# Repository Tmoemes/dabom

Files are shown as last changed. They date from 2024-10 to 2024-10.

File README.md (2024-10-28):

# Installation and Assembly Guide

## Disclaimer

The project was created by a team of students under the Adaptive Robotics minor at Fontys University of Applied Sciences. The goal of the project was to create a plug-and-play introduction to ROS 2 Humble and mobile robotics. By following the guide, anyone should be able to create their own holonomic platform and install all the necessary programs to create a map of the environment and autonomously navigate within the map.

## Hardware Guide

### 3D Printed Parts

All the 3D models are located inside the `CAD` folder. For 3D printing, use the `.stl` file format. You may use Fusion 360 to open the individual components and save them as `.stl`. STL (Standard Triangle Library) files are the most commonly used file format for 3D printing. These files need to be sliced by slicing software before the 3D printer can interpret them. For slicing, Cura slicer is recommended with the following print parameters:

| Print Parameters | Value |
| --- | --- |
| Material | Generic PLA |
| Print Temperature | 205°C |
| Print Speed | 50 mm/s or less (aim for good quality) |
| Layer Height | 0.1 or 0.12 mm |
| Wall Count | 3 |
| Bottom and Top Wall Count | 8 |
| Infill | 20% gyroid |
| Build Plate Adhesion | Brim (recommended) |

For printing, Ultimaker and Bambu Lab printers were used. These printers provide high quality; however, they are not mandatory for the project since the plastic parts are plenty strong by themselves.

For the mechanical assembly, a full CAD assembly is provided, which can be used as a reference.

### Electrical Components

All the necessary components are listed in the BOM (Bill of Materials) Excel file. A possible vendor is provided, but you are free to source the components from anywhere. It is important to mention that the Lidar used for this project, RPLidar model A2M8, is currently discontinued. The alternative A2M12 requires changes to the code. These changes are not implemented in the current working repository! The implementation of the A2M12 model is only recommended for experienced ROS users.

### Electrical Schematics



For the wiring of the power lines it is recommended to use the 0.5mm gauge wires with Farrell connectors on the end to make connections more safe and reliable. 
For details regarding the Arduino check [Arduino Wiring Schematics](Arduino_Code/README.md).

## Software Guide

### Computer Side
On the computer you want to install Ubuntu Desktop 22.04 LTS. For a guide how to install Ubuntu follow the link: [Install Ubuntu Guide](https://itsfoss.com/install-ubuntu/)Additionally it is recommended to download the Raspberry Pi etcher tool and use that instead of Rufus or Balena etcher since that tool will be necessary later for the Raspberry Pi imaging.

First we need to install git
```bash
sudo apt install git
```
Now we can go ahead and download the git

**Follow here from the Raspberry Pi**
The first step is to clone the GitHub repository:
```bash
git clone https://github.com/Tmoemes/dabom.git
```
Now that the GitHub is cloned we can show the folder and navigate within it. 

**It is important to install ROS 2 Humble which you can do by follow this guide [ROS Humble](https://docs.ros.org/en/humble/Installation/Ubuntu-Install-Debs.html) .  Make sure you install the desktop version on both.**

After which we need to install additional components for the system so run the following command: 
```bash
cd dabom
bash install.sh
```
During the installation prompts will pop up, by pressing enter you can continue the installation. Once it is done it is recommended to add the following line to the last line of the .bashrc file. 
```bash
ls -a 
nano .bashrc
```
and add the following line to the end of the text:
```bash 
source /opt/ros/humble/setup.bash
```

Once that is done we are going to navigate into the project and Colcon build it. Colcon building will make sure that the code is built into a ROS package, that can be run. Optionally a parameter could be added to the Colcon build, this way the project does not need to be recompiled after every change of the code.  
```bash 
cd dabom/dabom_ws
colcon build 
```
Optional:
```bash
cd dabom/dabom_ws
colcon build --symlink-install
```

After the build is finished you want to source the install file of the project. Make sure you are in the `dabom_ws` folder.
```bash
source install/setup.bash
```

Optionally you may also add this line to the `.bashrc` file. Just make sure you add the full location. Which means the line will look like this:
```bash
source dabom/dabom_ws/install/setup.bash
```
**End Raspberry Pi installation here**

Now we need to edit the startup file. Navigate to `dabom/dabom_ws/src/dabom_bringup/config` and edit the following file `/launch_config.yaml`. There you may enable or disable certain parts of the system. For example you may disable the external control input for the movement of the robot.

Now we can run the code on the computer side
```bash
ros2 launch dabom_bringup computer_bringup.py
```

### Raspberry Pi Side
[Ubuntu Installation Guide For Windows](https://roboticsbackend.com/install-ubuntu-on-raspberry-pi-without-monitor/)
Follow the installation manual and install Ubuntu Server 22.04.5 LTS onto an SD card. During the installation make sure that SSH is enabled. Make sure to remember the password! You can do this by overwriting the setting before installation. Further more make sure the Wi-Fi details are set to the address of a Wi-Fi network that both the computer/laptop and the Raspberry Pi will be connected to. For the Wi-Fi network it is possible to use a home router or a mobile hotspot with internet access enabled.  Once the installation is done plug in the SD card into the Raspberry Pi and provide power to the system.

Now connect your Ubuntu device to the same Wi-Fi network. Now it is necessary to figure out the IP address of the Raspberry PI. [How to discover devices on network?](https://www.tomshardware.com/how-to/scan-for-network-devices)
Now connect to the raspberry pi via SSH:
```bash
sudo ssh nameofthepi@ipaddress
```

Example:
```bash
sudo ssh pi@192.168.91.2
```

Now that we are in the Raspberry Pi terminal follow the same instructions as the Computer side.  

Before running the programs we have to make sure that the program has access to the serial ports, both for the lidar and the serial communication. Here make sure that the Lidar is plugged into ttyUSB0. On the Raspberry Pi that port is the top USB port furthest away from the Ethernet connector. 
For the Lidar:
```bash
cd src/rpldiar_ros/
source scripts/create_udev_rules.sh
```
For the serial communication:
```bash
cd dabom/dabom_ws/src/serial_comm
bash create_udev_rules.sh
```

If this would not work for some reason you may also run the following commands as a backup:
```bash
sudo chmod 777 /dev/ttyUSB0
sudo chmod 777 /dev/ttyS0
```

Now that the permissions are settled we can proceed with the launching of the robot software! Furthermore for some reason TAB auto complete is not working on the following command. Do this from inside the `dabom_ws` folder.
```bash
source /opt/ros/humble/setup.bash
source install/setup.bash
ros2 launch dabom_bringup rpi_bringup.py
```
If no error is returned the robot code should be up and running, you may exit the code any time by pressing `Ctrl + C` . 

# Operation of the robot:
Depending on which modes you enable in the startup file the robot can be controlled by an Xbox controller. As well as by RVIZ2, which is a GUI automatically turned on when you launch the computer side bring up. In RVIZ2 you may set Nav2 Goals, if you do so the robot navigates there autonomously.

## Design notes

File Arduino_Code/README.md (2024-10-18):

# Hardware Installation Instructions
## Software install
### Step-by-Step Guide to Install and Upload the Project using PlatformIO

1. **Install PlatformIO:**
    - Download and install [Visual Studio Code](https://code.visualstudio.com/).
    - Open Visual Studio Code and go to the Extensions view by clicking on the square icon in the sidebar or pressing `Ctrl+Shift+X`.
    - Search for "PlatformIO IDE" and click "Install".

2. **Open the Project in Visual Studio Code:**
    - Open Visual Studio Code.
    - Click on `File` > `Open Folder...` and select the `Arduino_Code` directory from the cloned repository.

3. **Install Dependencies:**
    - Open the PlatformIO Home by clicking on the house icon in the sidebar.
    - Click on "Open Project" and select the `Arduino_Code` directory.
    - PlatformIO will automatically detect the `platformio.ini` file and install the necessary dependencies.

4. **Configure the Project:**
    - Open the `platformio.ini` file in the `Arduino_Code` directory.
    - Ensure the configuration matches your setup. For example:
      ```ini
      [env:megaatmega2560]
        platform = atmelavr
        board = megaatmega2560
        framework = arduino
        monitor_speed = 19200
        lib_deps = 
	        paulstoffregen/Encoder@^1.4.4
      ```

5. **Upload the Code to Arduino Mega:**
    - Connect your Arduino Mega to your computer using a USB cable.
    - In Visual Studio Code, open the PlatformIO sidebar by clicking on the alien icon.
    - Click on the "Upload" button (arrow pointing right) to compile and upload the code to the Arduino Mega.

6. **Monitor Serial Output (Optional):**
    - To monitor the serial output from the Arduino, click on the "Serial Monitor" button (plug icon) in the PlatformIO sidebar.
    - Ensure the baud rate matches the one set in your code (e.g., `19200`).

Your project should now be uploaded to the Arduino Mega and running as expected.

## Wiring for Power and Signals

### Arduino <-> Raspberry Pi Communication
The Pi and Arduino communicate using the hardware serial of the Pi to the Serial2 of the Arduino Mega.
In this case we are also powering the Arduino from the Pi 5V pins.
Make sure the Pi and Arduino are grounded together for serial communication to funcion properly 
1. **Raspberry Pi GPIO Connections:**
    - `GPIO 14 (TXD)` to `Arduino Pin 16 (TX2)`
    - `GPIO 15 (RXD)` to `Arduino Pin 17 (RX2)`

### Example Wiring Diagram for Arduino <-> Raspberry Pi Communication
```
+------------------+       +------------------+
| Raspberry Pi     |       | Arduino Mega     |
|                  |       |                  |
|   GPIO 14 (TXD)  +------>+ 17 (RX2)         |
|   GPIO 15 (RXD)  +------>+ 16 (TX2)         |
+------------------+       +------------------+
```

### Motor and Encoder Connections
For the motors, it is necessary to connect the `EN` connection to PWM-capable pins to modulate speed. On the Arduino Mega, the PWM-capable pins are `D2-D13` and `D44-D46`.

For the encoders, it is important to connect at least one of the channels to an interrupt-capable pin. The Arduino Mega has 6 available interrupts:
- `INT.0` on Pin `21`
- `INT.1` on Pin `20`
- `INT.2` on Pin `19`
- `INT.3` on Pin `18`
- `INT.4` on Pin `2`
- `INT.5` on Pin `3`

Make sure the Arduino is grounded together with the motor drivers and the encoders to ensure proper signaling.

1. **Motor Connections:**  
    - **Motor 0 (Front Left):**
        - `EN` pin to `D2`
        - `IN1` pin to `D35`
        - `IN2` pin to `D37`
    - **Motor 1 (Front Right):**
        - `EN` pin to `D3`
        - `IN1` pin to `D41`
        - `IN2` pin to `D39`
    - **Motor 2 (Back Left):**
        - `EN` pin to `D4`
        - `IN1` pin to `D31`
        - `IN2` pin to `D33`
    - **Motor 3 (Back Right):**
        - `EN` pin to `D5`
        - `IN1` pin to `D45`
        - `IN2` pin to `D43`

2. **Encoder Connections:**
    - **Encoder 0 (Front Left):**
        - `A` pin to `D18`
        - `B` pin to `D23`
    - **Encoder 1 (Front Right):**
        - `A` pin to `D19`
        - `B` pin to `D25`
    - **Encoder 2 (Back Left):**
        - `A` pin to `D20`
        - `B` pin to `D27`
    - **Encoder 3 (Back Right):**
        - `A` pin to `D21`
        - `B` pin to `D29`

### Example Wiring Diagram for Motors and Encoders
```
+------------------+       +------------------+
| Motor 0          |       | Arduino          |
|                  |       |                  |
|   EN             +------>+ D2               |
|   IN1            +------>+ D35              |
|   IN2            +------>+ D37              |
+------------------+       +------------------+

+------------------+       +------------------+
| Encoder 0        |       | Arduino          |
|                  |       |                  |
|   A              +------>+ D18              |
|   B              +------>+ D23              |
+------------------+       +------------------+

+------------------+       +------------------+
| Motor 1          |       | Arduino          |
|                  |       |                  |
|   EN             +------>+ D3               |
|   IN1            +------>+ D41              |
|   IN2            +------>+ D39              |
+------------------+       +------------------+

+------------------+       +------------------+
| Encoder 1        |       | Arduino          |
|                  |       |                  |
|   A              +------>+ D19              |
|   B              +------>+ D25              |
+------------------+       +------------------+

+------------------+       +------------------+
| Motor 2          |       | Arduino          |
|                  |       |                  |
|   EN             +------>+ D4               |
|   IN1            +------>+ D31              |
|   IN2            +------>+ D33              |
+------------------+       +------------------+

+------------------+       +------------------+
| Encoder 2        |       | Arduino          |
|                  |       |                  |
|   A              +------>+ D20              |
|   B              +------>+ D27              |
+------------------+       +------------------+

+------------------+       +------------------+
| Motor 3          |       | Arduino          |
|                  |       |                  |
|   EN             +------>+ D5               |
|   IN1            +------>+ D45              |
|   IN2            +------>+ D43              |
+------------------+       +------------------+

+------------------+       +------------------+
| Encoder 3        |       | Arduino          |
|                  |       |                  |
|   A              +------>+ D21              |
|   B              +------>+ D29              |
+------------------+       +------------------+
```

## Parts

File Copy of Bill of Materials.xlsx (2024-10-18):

Bill of Material
Item # | Description | Vendor | Part Number | Qty | Cost | Link to Where to Purchase
1 | Arduino Uno R3 with DIP | Amazon | Uno R3 | 1 | $21.95 | http://www.amazon.com/Arduino-UNO-board-DIP-ATmega328P/dp/B006H06TVG
2 | raspberry pi 4 8gb |  |  | 1 | $81.77
3 | Mechanum wheels | Amazon |  | 4 | $29.95 | https://www.amazon.nl/Mecanum-wiel-omni-directionele-Auto-onderdelen-Accessoires-DIY-speelgoedcomponenten/dp/B08VFLDJR9
4 | RPlidar | Amazon | A2M8 | 1 | $599.54 | https://www.amazon.nl/-/en/RPLIDAR-A2M8-360%C2%B0-laser-scanner/dp/B01L1T32PI
5 | RPlidar (Potential replacement due to retirement of A2m8 LIDAR) | antratek | A2M12 | 1 | $277.99 | https://www.antratek.nl/rplidar-a2m12-360-laser-range-scanner
6 | l298n motor driver |  |  | 2 | $6.99 | https://www.amazon.nl/DollaTek-Stepper-Controller-verdubbeling-Smart-auto-robot/dp/B07DK6Q8F9
7 | BUCK converter at least 5A | Amazon |  | 1 | $7,49 | https://www.amazon.nl/JZK-Verstelbare-Converter-constante-Regulator/dp/B09TT1Q739
8 | 0,5mm wires |  |  | ~2m
9 | Male to Female Dupont jumper wires |  |  | 40 | $7.99 | https://www.amazon.nl/Dupont-Jumper-Arduino-Raspberry-projects/dp/B09KGRM98K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

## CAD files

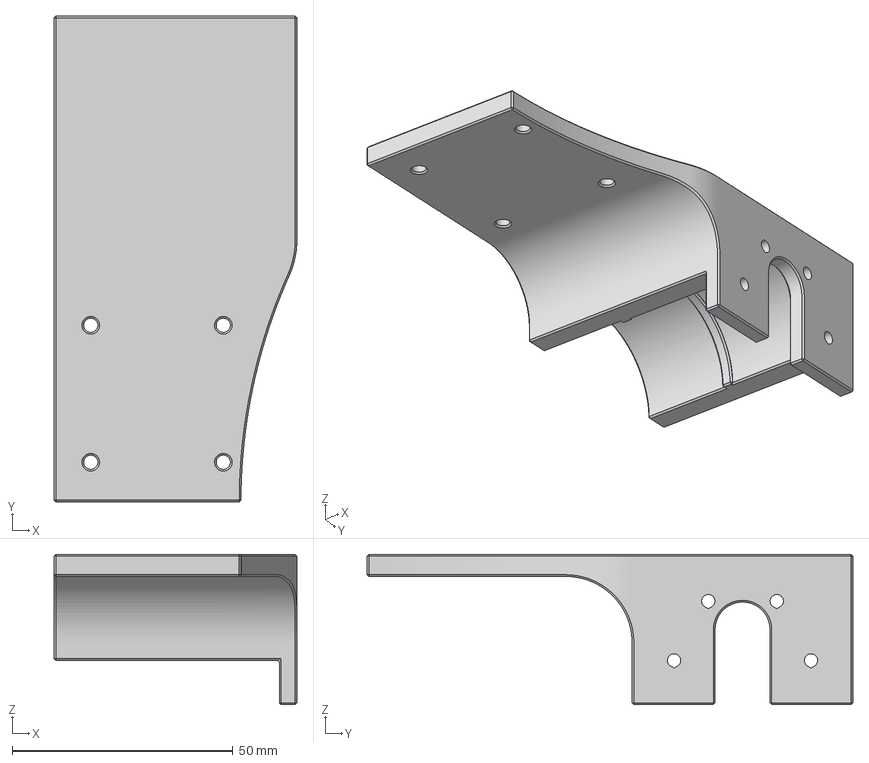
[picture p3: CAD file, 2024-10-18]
CAD/MotorMountD.3mf
55.0 x 110.0 x 34.0 mm

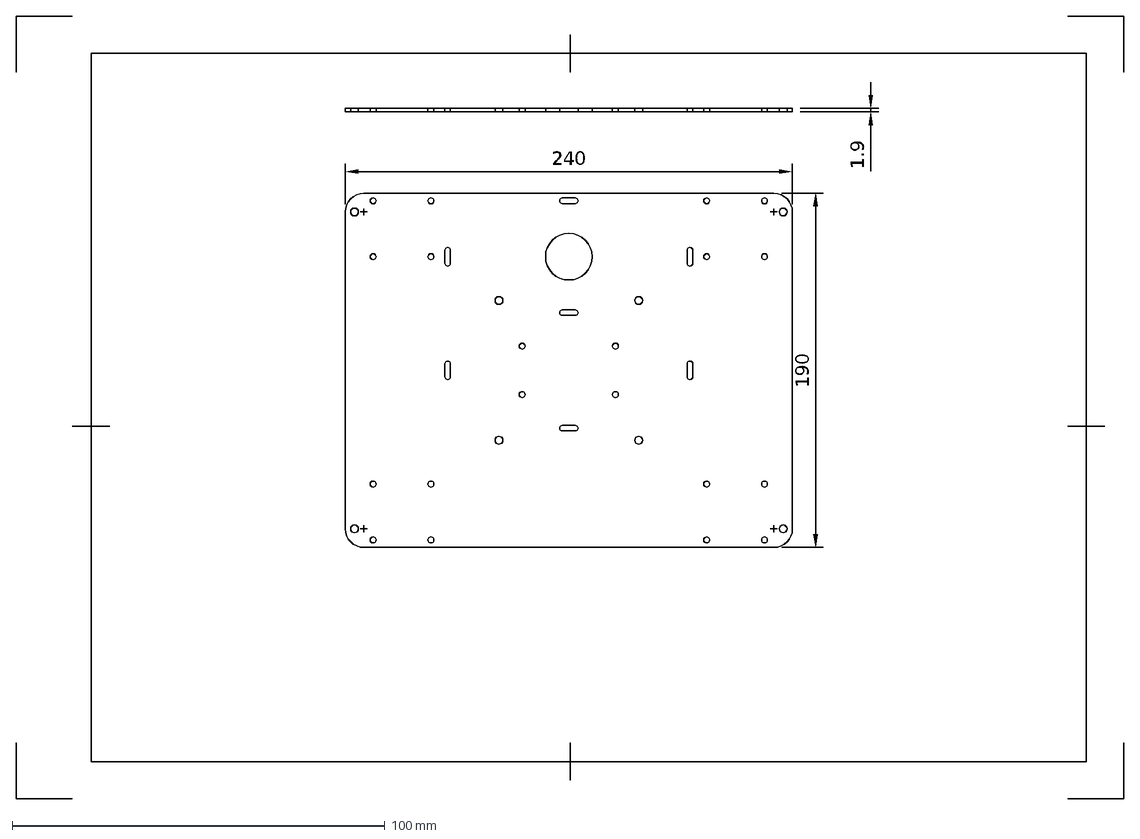
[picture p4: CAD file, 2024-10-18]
CAD/Base_Plate.dxf
240
190
1.9

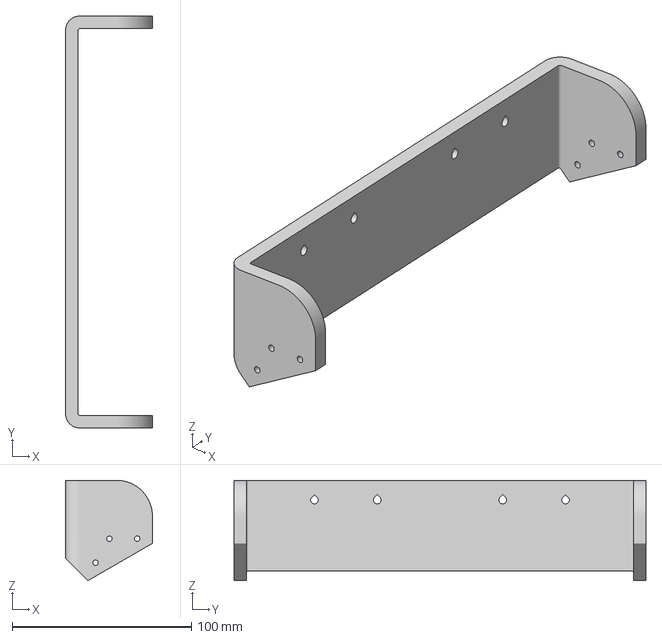
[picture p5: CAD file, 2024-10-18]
CAD/C_Karg_Brace.3mf
48.4 x 229.8 x 56.0 mm

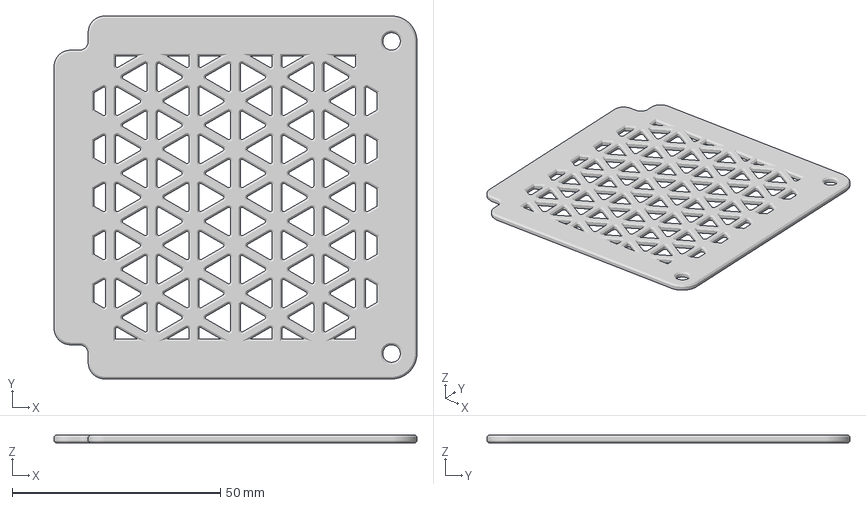
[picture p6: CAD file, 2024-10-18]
CAD/WirePlate.3mf
87.2 x 87.2 x 2.00 mm

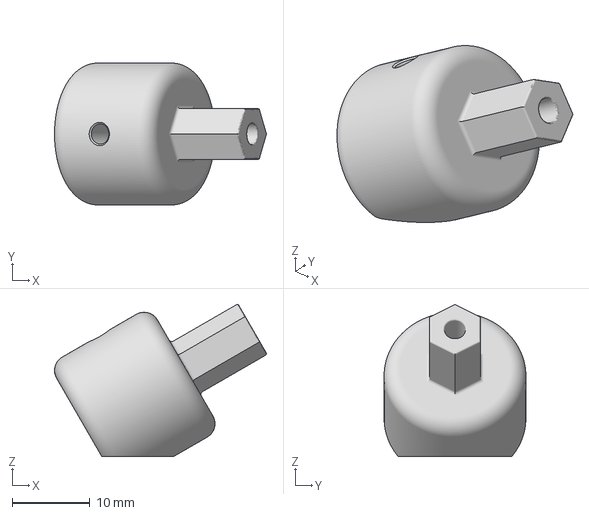
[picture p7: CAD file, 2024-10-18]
CAD/WheelHubAddapter2.6mmHole.3mf
27.3 x 18.2 x 19.6 mm

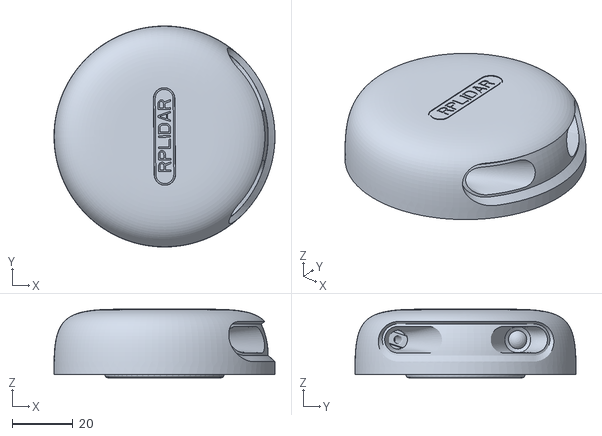
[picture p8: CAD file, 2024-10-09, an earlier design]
dabom_ws/src/dabomb_description/meshes/LIDAR_1.stl
72.5 x 72.5 x 22.5

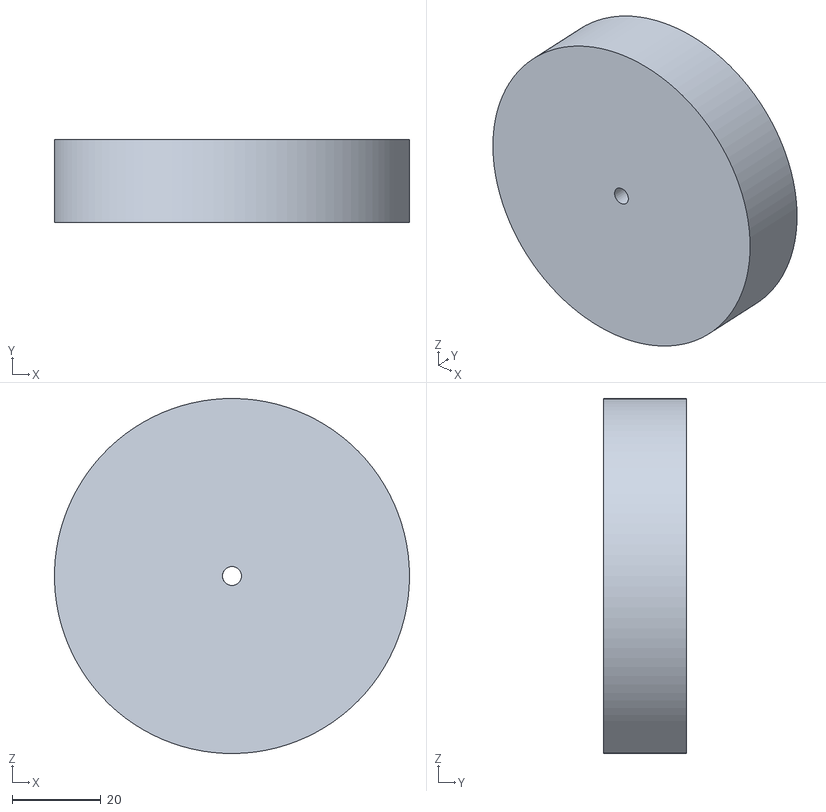
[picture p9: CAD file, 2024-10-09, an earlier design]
dabom_ws/src/dabomb_description/meshes/Wheel2_1.stl
80.0 x 18.7 x 80.0

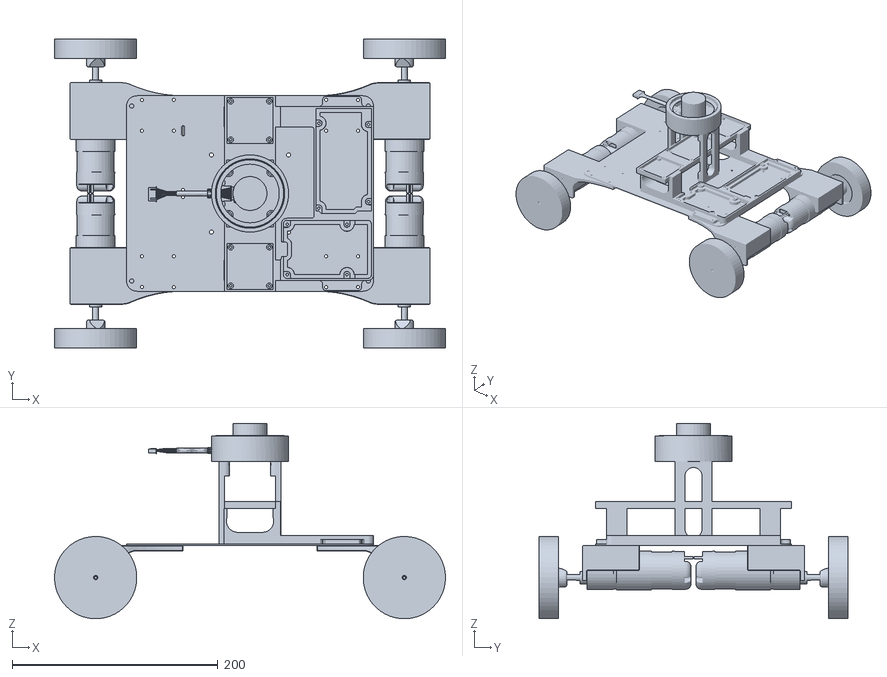
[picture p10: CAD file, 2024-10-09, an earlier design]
dabom_ws/src/dabomb_description/meshes/base_link.stl
380.0 x 300.0 x 190.0

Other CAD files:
dabom_ws/src/install/dabomb_description/share/dabomb_description/meshes/LIDAR_1.stl
dabom_ws/src/install/dabomb_description/share/dabomb_description/meshes/base_link.stl
CAD/MotorMountB.3mf
dabom_ws/src/install/dabomb_description/share/dabomb_description/meshes/Wheel4_1.stl
CAD/MotorMountA.3mf
dabom_ws/src/install/dabomb_description/share/dabomb_description/meshes/Wheel3_1.stl
CAD/MotorMountC.3mf
dabom_ws/src/install/dabomb_description/share/dabomb_description/meshes/Wheel2_1.stl
dabom_ws/src/install/dabomb_description/share/dabomb_description/meshes/Wheel1_1.stl
dabom_ws/src/dabomb_description/meshes/Wheel4_1.stl
CAD/Base_Plate.dwg
dabom_ws/src/dabomb_description/meshes/Wheel1_1.stl
dabom_ws/src/dabomb_description/meshes/Wheel3_1.stl

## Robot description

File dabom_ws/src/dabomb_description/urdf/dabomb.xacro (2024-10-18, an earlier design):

<?xml version="1.0" ?>
<robot name="dabomb" xmlns:xacro="http://www.ros.org/wiki/xacro">

<material name="gray">
  <color rgba="0.75 0.75 0.75 1.0"/>  <!-- This is gray with full opacity -->
</material>


<xacro:include filename="$(find dabomb_description)/urdf/materials.xacro" />
<xacro:include filename="$(find dabomb_description)/urdf/dabomb.trans" />
<xacro:include filename="$(find dabomb_description)/urdf/dabomb.gazebo" />
<link name="base_footprint" />

<link name="base_link">
  <inertial>
    <origin xyz="0.001965778230803289 0.00012164122075361151 0.06076837613584456" rpy="0 0 0"/>
    <mass value="3.2995710672768235"/>
    <inertia ixx="0.032808" iyy="0.061307" izz="0.086932" ixy="-3.2e-05" iyz="-8e-06" ixz="-8.9e-05"/>
  </inertial>
  <visual>
    <origin xyz="0 0 -0.04" rpy="0 0 0"/>
    <geometry>
      <mesh filename="file://$(find dabomb_description)/meshes/base_link.stl" scale="0.001 0.001 0.001"/>
    </geometry>
    <material name="gray"/>
  </visual>
  <collision>
    <origin xyz="0 0 -0.04" rpy="0 0 0"/>
    <geometry>
      <mesh filename="file://$(find dabomb_description)/meshes/base_link.stl" scale="0.001 0.001 0.001"/>
    </geometry>
  </collision>
</link>

<link name="Wheel1_1">
  <inertial>
    <origin xyz="3.605747672386084e-07 0.00934999998147884 -8.583050173371909e-10" rpy="0 0 0"/>
    <mass value="0.7357403909763499"/>
    <inertia ixx="0.000317" iyy="0.00059" izz="0.000317" ixy="-0.0" iyz="0.0" ixz="0.0"/>
  </inertial>
  <visual>
    <origin xyz="-0.15 -0.15 -0.04" rpy="0 0 0"/>
    <geometry>
      <mesh filename="file://$(find dabomb_description)/meshes/Wheel1_1.stl" scale="0.001 0.001 0.001"/>
    </geometry>
    <material name="gray"/>
  </visual>
  <collision>
    <origin xyz="-0.15 -0.15 -0.04" rpy="0 0 0"/>
    <geometry>
      <mesh filename="file://$(find dabomb_description)/meshes/Wheel1_1.stl" scale="0.001 0.001 0.001"/>
    </geometry>
  </collision>
</link>

<link name="Wheel3_1">
  <inertial>
    <origin xyz="-3.6057476762718643e-07 0.00934999998147884 -8.583049965205092e-10" rpy="0 0 0"/>
    <mass value="0.7357403909763499"/>
    <inertia ixx="0.000317" iyy="0.00059" izz="0.000317" ixy="-0.0" iyz="0.0" ixz="0.0"/>
  </inertial>
  <visual>
    <origin xyz="0.15 -0.15 -0.04" rpy="0 0 0"/>
    <geometry>
      <mesh filename="file://$(find dabomb_description)/meshes/Wheel3_1.stl" scale="0.001 0.001 0.001"/>
    </geometry>
    <material name="gray"/>
  </visual>
  <collision>
    <origin xyz="0.15 -0.15 -0.04" rpy="0 0 0"/>
    <geometry>
      <mesh filename="file://$(find dabomb_description)/meshes/Wheel3_1.stl" scale="0.001 0.001 0.001"/>
    </geometry>
  </collision>
</link>

<link name="Wheel2_1">
  <inertial>
    <origin xyz="3.605747672386084e-07 -0.00934999998147884 -8.583056140820666e-10" rpy="0 0 0"/>
    <mass value="0.7357403909763499"/>
    <inertia ixx="0.000317" iyy="0.00059" izz="0.000317" ixy="0.0" iyz="-0.0" ixz="-0.0"/>
  </inertial>
  <visual>
    <origin xyz="-0.15 0.15 -0.04" rpy="0 0 0"/>
    <geometry>
      <mesh filename="file://$(find dabomb_description)/meshes/Wheel2_1.stl" scale="0.001 0.001 0.001"/>
    </geometry>
    <material name="gray"/>
  </visual>
  <collision>
    <origin xyz="-0.15 0.15 -0.04" rpy="0 0 0"/>
    <geometry>
      <mesh filename="file://$(find dabomb_description)/meshes/Wheel2_1.stl" scale="0.001 0.001 0.001"/>
    </geometry>
  </collision>
</link>

<link name="Wheel4_1">
  <inertial>
    <origin xyz="-3.6057476762718643e-07 -0.00934999998147884 -8.583055516320215e-10" rpy="0 0 0"/>
    <mass value="0.7357403909763499"/>
    <inertia ixx="0.000317" iyy="0.00059" izz="0.000317" ixy="0.0" iyz="-0.0" ixz="-0.0"/>
  </inertial>
  <visual>
    <origin xyz="0.15 0.15 -0.04" rpy="0 0 0"/>
    <geometry>
      <mesh filename="file://$(find dabomb_description)/meshes/Wheel4_1.stl" scale="0.001 0.001 0.001"/>
    </geometry>
    <material name="gray"/>
  </visual>
  <collision>
    <origin xyz="0.15 0.15 -0.04" rpy="0 0 0"/>
    <geometry>
      <mesh filename="file://$(find dabomb_description)/meshes/Wheel4_1.stl" scale="0.001 0.001 0.001"/>
    </geometry>
  </collision>
</link>

<link name="laser">
  <inertial>
    <origin xyz="0.0039907248324316845 -0.00022724344297910342 -0.002459373991692604" rpy="0 0 0"/>
    <mass value="0.2649835736448253"/>
    <inertia ixx="8.2e-05" iyy="8.5e-05" izz="0.000145" ixy="-0.0" iyz="0.0" ixz="-2e-06"/>
  </inertial>
  <visual>
    <origin xyz="0.0 -0.0 -0.19" rpy="0 0 0"/>
    <geometry>
      <mesh filename="file://$(find dabomb_description)/meshes/LIDAR_1.stl" scale="0.001 0.001 0.001"/>
    </geometry>
    <material name="gray"/>
  </visual>
  <collision>
    <origin xyz="0.0 -0.0 -0.19" rpy="0 0 0"/>
    <geometry>
      <mesh filename="file://$(find dabomb_description)/meshes/LIDAR_1.stl" scale="0.001 0.001 0.001"/>
    </geometry>
  </collision>
</link>

<joint name="base_joint" type="fixed">
  <origin xyz="0.0 0.0 0.04" rpy="0 0 0"/>
  <parent link="base_footprint"/>
  <child link="base_link"/>
</joint>

<joint name="Wheel1" type="continuous">
  <origin xyz="0.15 0.15 0.0" rpy="0 0 0"/>
  <parent link="base_link"/>
  <child link="Wheel1_1"/>
  <axis xyz="-0.0 1.0 0.0"/>
</joint>

<joint name="Wheel3" type="continuous">
  <origin xyz="-0.15 0.15 0.0" rpy="0 0 0"/>
  <parent link="base_link"/>
  <child link="Wheel3_1"/>
  <axis xyz="0.0 1.0 0.0"/>
</joint>

<joint name="Wheel2" type="continuous">
  <origin xyz="0.15 -0.15 0.0" rpy="0 0 0"/>
  <parent link="base_link"/>
  <child link="Wheel2_1"/>
  <axis xyz="-0.0 -1.0 0.0"/>
</joint>

<joint name="Wheel4" type="continuous">
  <origin xyz="-0.15 -0.15 0.0" rpy="0 0 0"/>
  <parent link="base_link"/>
  <child link="Wheel4_1"/>
  <axis xyz="0.0 -1.0 0.0"/>
</joint>

<joint name="laser_joint" type="fixed">
  <origin xyz="0.0 0.0 0.15" rpy="0 0 ${pi}"/>
  <parent link="base_link"/>
  <child link="laser"/>
</joint>

</robot>

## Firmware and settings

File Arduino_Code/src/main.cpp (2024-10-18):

#include <Arduino.h>
#include "config.h"

void processSerialInput(HardwareSerial &thisserial);
void getSerialInput();
void printMotorInfo();
void sendEncoder();

long currentTime = 0;

// debug output timing
long d_previousTime = 0;

// pi comm timing
long p_previousTime = 0;

long lastReceivedTime = 0;

void setup()
{
  // Used to display debug information
  Serial.begin(DEBUG_BAUD_RATE);

  // Serial for communication with Raspberry Pi
  Serial2.begin(PI_BAUD_RATE);

  lastReceivedTime = millis();
  // Wait for Serial Monitor to be opened
  while (!Serial || !Serial2)
  {
    // do nothing
  }
  Serial.println("Serial Ready");

  for (size_t i = 0; i < 4; i++)
  {
    motors[i].begin();
    Serial.println("Motor ");
    Serial.print(i);
    Serial.println(" started");
  }

  Serial.println("Setup Complete");
}

void loop()
{
  currentTime = millis();

  if (currentTime - d_previousTime >= DEBUG_FREQ && DEBUG_FREQ != 0)
  {
    printMotorInfo();
    d_previousTime = currentTime;
  }

  if (currentTime - lastReceivedTime >= PI_COMM_TIMEOUT)
  {
    Serial.println("No command received, stopping motors");
    lastReceivedTime = currentTime;
    for (int i = 0; i < 4; i++)
    {
      motors[i].stop();
    }
  }

  if (currentTime - p_previousTime >= PI_COMM_FREQ)
  {

    p_previousTime = currentTime;
    sendEncoder();
  }

  // processSerialInput(Serial);
  processSerialInput(Serial2);
}

void processSerialInput(HardwareSerial &thisserial)
{
  if (thisserial.available())
  {
    char input[32] = {0};
    thisserial.readBytesUntil('\n', input, 31);
    input[31] = '\0';                   // Ensure null-terminated string
    char *command = strtok(input, " "); // tokenise input on spaces
    if (command != nullptr && strcmp(command, "m") == 0)
    {
      char *motorStr = strtok(NULL, " ");
      char *speedStr = strtok(NULL, " ");
      if (motorStr != nullptr && speedStr != nullptr)
      {

        unsigned int motor = atoi(motorStr);

        // check if motor number is valid
        if (motor < 0 || motor >= sizeof(motors) / sizeof(Motor))
        {
          Serial.println("Invalid motor number");
          return;
        }

        // convert speed string to double
        double speed = atof(speedStr);

        // map input speed to 0-255
        int targetSpeed = map(abs(speed), 0, 10, 50, 255);

        // set motor speed and direction
        motors[motor].setSpeed(targetSpeed);
        if (speed > 0){motors[motor].forward();}
        else if (speed < 0){motors[motor].backward();}
        else{motors[motor].stop();}

        // update last received time
        lastReceivedTime = currentTime;
      }
      else
      {
        Serial.println("Invalid input format");
      }
    }
    else
    {
      // Serial.print("Unknown command: ");
      // Serial.print(input);
      // Serial.println();
    }
  }
}

void printMotorInfo()
{
  char message[320] = {0};
  int x = snprintf(message, sizeof(message), "\nCurrent motor Values---------------\n");
  for (size_t i = 0; i < 4; i++)
  {
    long count = motors[i].readEncoder();
    double speed = motors[i].getSpeed();
    x += snprintf(message + x, sizeof(message), "Motor %i: \n-Speed: %d \n-Encoder Value: %li\n",i, speed, count);
    Serial.print(message);
  }
}

void sendEncoder()
{
  long count = motors[0].readEncoder();
  long count1 = motors[1].readEncoder();
  long count2 = motors[2].readEncoder();
  long count3 = motors[3].readEncoder();

  char message[64] = {0};
  snprintf(message, sizeof(message), "%li,%li,%li,%li", count, count1, count2, count3);
  Serial2.println(message);
}

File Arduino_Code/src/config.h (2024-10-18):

#ifndef CONFIG_H
#define CONFIG_H
#include "motor.h"
#include <Encoder.h>

// PI COMM constants
#define PI_COMM_FREQ 20
#define PI_COMM_TIMEOUT 300
#define PI_BAUD_RATE 38400

// DEBUG constants
#define DEBUG_FREQ 1000 // time in ms between debug prints, 0 to disable
#define DEBUG_BAUD_RATE 19200

// Motor 0:Front left
#define MOTOR0_PIN_EN 2 
#define MOTOR0_PIN_IN1 35
#define MOTOR0_PIN_IN2 37
#define ENCODER0_PIN_A 18 // INT.3 on Pin 18
#define ENCODER0_PIN_B 23   

// Motor 1: Front right
#define MOTOR1_PIN_EN 3
#define MOTOR1_PIN_IN1 41
#define MOTOR1_PIN_IN2 39
#define ENCODER1_PIN_A 19 // INT.2 on pin 19
#define ENCODER1_PIN_B 25

// Motor 2: Back left
#define MOTOR2_PIN_EN 4
#define MOTOR2_PIN_IN1 31
#define MOTOR2_PIN_IN2 33
#define ENCODER2_PIN_A 20 // INT.1 on pin 20
#define ENCODER2_PIN_B 27
 
// Motor 3: Back right
#define MOTOR3_PIN_EN 5
#define MOTOR3_PIN_IN1 45
#define MOTOR3_PIN_IN2 43
#define ENCODER3_PIN_A 21 // INT.0 on Pin 21
#define ENCODER3_PIN_B 29

// Defining and setting up the motors and encoders
Encoder enc0(ENCODER0_PIN_A, ENCODER0_PIN_B);
Encoder enc1(ENCODER1_PIN_A, ENCODER1_PIN_B);
Encoder enc2(ENCODER2_PIN_A, ENCODER2_PIN_B);
Encoder enc3(ENCODER3_PIN_A, ENCODER3_PIN_B);

Motor m0(MOTOR0_PIN_EN, MOTOR0_PIN_IN1, MOTOR0_PIN_IN2, enc0, true);
Motor m1(MOTOR1_PIN_EN, MOTOR1_PIN_IN1, MOTOR1_PIN_IN2, enc1);
Motor m2(MOTOR2_PIN_EN, MOTOR2_PIN_IN1, MOTOR2_PIN_IN2, enc2, true);
Motor m3(MOTOR3_PIN_EN, MOTOR3_PIN_IN1, MOTOR3_PIN_IN2, enc3);

Motor motors[] = {m0,m1,m2,m3};

#endif // CONFIG_H

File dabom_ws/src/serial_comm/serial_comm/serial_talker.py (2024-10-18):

from geometry_msgs.msg import TwistStamped
import rclpy
from rclpy.node import Node
import serial


class Serial_Talker(Node):

    def __init__(self):
        super().__init__('Serial_Talker')

        # Declare parameters with default values
        self.declare_parameter('timer_period', 0.2)
        self.declare_parameter('port', '/dev/ttyS0')
        self.declare_parameter('baudrate', 38400)
        self.declare_parameter('timeout', 0.01)
        self.declare_parameter('pulses_per_rev', 1440)
        self.declare_parameter('wheel_radius', 0.08)

        # Create a subscription to the /motor_vel topic
        self.subscription = self.create_subscription(TwistStamped, '/motor_vel', self.motor_vel_callback, 1)

        # Create a publisher to the /arduino_vel topic
        self.publisher_ = self.create_publisher(TwistStamped, '/arduino_vel', 1)
        
        # Get the timer period parameter and create a timer
        timer_period = self.get_parameter('timer_period').get_parameter_value().double_value
        self.timer = self.create_timer(timer_period, self.arduino_vel_callback)

        # Get serial communication parameters
        self.port = self.get_parameter('port').get_parameter_value().string_value   
        self.baudrate = self.get_parameter('baudrate').get_parameter_value().integer_value
        self.timeout = self.get_parameter('timeout').get_parameter_value().double_value


        # Initialize serial communication
        self.serial_port = serial.Serial(
            port=self.port,
            baudrate=self.baudrate,
            timeout=self.timeout,
            write_timeout=self.timeout,
        )

        # Initialize variables for velocity calculation
        self.last_time = self.get_clock().now()
        self.pulses_per_rev = self.get_parameter('pulses_per_rev').get_parameter_value().integer_value
        self.wheel_radius = self.get_parameter('wheel_radius').get_parameter_value().double_value
        self.last_encoder_values = [0, 0, 0, 0]

    def arduino_vel_callback(self):
        serial_read = None
        try:
            serial_read = self.serial_port.readline().strip()
            # self.get_logger().info('receiving: "%s"' % serial_read)
            
        except serial.SerialException:
            # Log an error if there is an issue reading from the serial port
            self.get_logger().error('Error reading from serial port')
            # Reinitialize the serial port
            self.serial = serial.Serial(
                port=self.port,
                baudrate=self.baudrate,
                timeout=self.timeout,
                write_timeout=self.timeout
            )
        if serial_read:
            try:
                # Parse the encoder values from the serial data
                encoder_values = str(serial_read)[2:-1].split(',')
                if len(encoder_values) != 4:
                    raise Exception('Incorrect number of encoder values')
                for i in range(4):
                    encoder_values[i] = float(encoder_values[i])
            except Exception as e:
                self.get_logger().error('Error parsing serial data')
                return
            # self.get_logger().info('read encoder val: "%s"' % encoder_values)
            calculated_velocities = self.calculate_velocities(encoder_values)
            # self.get_logger().info('calculated vel: "%s"' % calculated_velocities)
            msg = TwistStamped()
            msg.twist.linear.x = calculated_velocities[0]
            msg.twist.linear.y = calculated_velocities[1]
            msg.twist.linear.z = calculated_velocities[2]
            msg.twist.angular.x = calculated_velocities[3]
            self.publisher_.publish(msg)
            

    def calculate_velocities(self, encoder_values):
        current_time = self.get_clock().now()
        delta_time = (current_time - self.last_time).nanoseconds / 1e9
        self.last_time = current_time
        angular_velocities = [0, 0, 0, 0]
        for i in range(4):
            encoder_diff = encoder_values[i] - self.last_encoder_values[i]
            angular_velocities[i] = (encoder_diff / self.pulses_per_rev) * 2 * 3.14159 / delta_time
        self.last_encoder_values = encoder_values
        return angular_velocities
        
    def send_serial_data(self, data):
        if self.serial_port.is_open:
            try:
                # self.serial_port.reset_output_buffer()
                # self.get_logger().info('sending: "%s"' % data.encode())
                self.serial_port.write(data.encode())
            except serial.SerialException:
                self.get_logger().error('Error writing to serial port')
                self.serial = serial.Serial(
                    port=self.port,
                    baudrate=self.baudrate,
                    timeout=self.timeout,
                    write_timeout=self.timeout
                )

    def motor_vel_callback(self, msg):
        motor_vels = [msg.twist.linear.x, msg.twist.linear.y,msg.twist.linear.z, msg.twist.angular.x]
        # Send the message over the serial port
        for i in range(4):
            serial_message = f'm {i} {str(round(motor_vels[i],3))}\n'
            # self.get_logger().info('sending: "%s"' % serial_message)
            self.send_serial_data(serial_message)
        
def main(args=None):
    rclpy.init(args=args)

    serial_talker = Serial_Talker()

    rclpy.spin(serial_talker)

    serial_talker.destroy_node()
    rclpy.shutdown()


if __name__ == '__main__':
    main()

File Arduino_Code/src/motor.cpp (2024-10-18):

#include "motor.h"

Motor::Motor(int enA, int in1, int in2, Encoder &encoder, bool inverted)
    : _enA(enA), _in1(in1), _in2(in2), _encoder(encoder), _inverted(inverted), _encoderCount(0) {}

void Motor::begin()
{
    pinMode(_enA, OUTPUT);
    pinMode(_in1, OUTPUT);
    pinMode(_in2, OUTPUT);
}

void Motor::setSpeed(int speed)
{
    analogWrite(_enA, abs(speed));
}

void Motor::forward()
{
    digitalWrite(_in1, HIGH);
    digitalWrite(_in2, LOW);
}

void Motor::backward()
{
    digitalWrite(_in1, LOW);
    digitalWrite(_in2, HIGH);
}

void Motor::stop()
{
    digitalWrite(_in1, LOW);
    digitalWrite(_in2, LOW);
}


/// @brief 
/// @return (long) encoder count value
long Motor::readEncoder()
{
    return _inverted ? _encoder.read() * -1 : _encoder.read();
}

/// @brief sets encoder count to 0
void Motor::resetEncoder()
{
    _encoder.write(0);
}

/// @brief get the speed of the motor according to encoder readings
/// @return angular velocity (rad/s)
double Motor::getSpeed()
{
    long currentTime = millis();
    long elapsedTime = currentTime - _lastTime;
    long currentPosition = _encoderCount;
    long deltaPosition = currentPosition - _lastPosition;
    double speed = (double)deltaPosition / elapsedTime;
    _lastTime = currentTime;
    _lastPosition = currentPosition;
    return speed;
}

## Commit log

2024-10-09 added starting ws
    [LIDAR_1.stl, Wheel1_1.stl, Wheel2_1.stl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]
2024-10-10 Add: Lidar description.txt
2024-10-10 angular velocities of wheels dont have to be pretranslated to linear velocities this is done by the forward kin, the angle should be wrapped between 0 and 2pi
2024-10-10 Adding the joint state node
2024-10-10 we are publishing our own joint states so no joint_state_publisher needed
2024-10-10 fixed unique joint state launch
2024-10-10 updated serial and added arduino code
2024-10-10 serial out of range fix
    [serial_talker.py]
2024-10-10 update arduino code
2024-10-10 remove debug after fix
    [main.cpp, serial_talker.py]
2024-10-10 velocities debug
2024-10-10 Should have corrected the warning/issue with gazebo.
    [dabomb.xacro]
2024-10-11 short circuit backward kinematics directly to odom. To test odom and check the alignments
2024-10-11 fix error with error handling
    [serial_talker.py]
2024-10-11 increade velocity frequency
2024-10-11 remove debug printing
2024-10-11 slow serial to 50hz
2024-10-11 stop exception handling from crashing
    [serial_talker.py]
2024-10-11 removed second joint state publisher
2024-10-11 Revert "short circuit backward kinematics directly to odom. To test odom and check the alignments"
    This reverts commit 5bc59cbdd3e449a41fe6b1332320c5ae745198fb.
2024-10-11 footprint reroll
2024-10-11 rotated laser forwards
    [dabomb.xacro]
2024-10-11 aaded euler to quaternion
    [dabomb.xacro]
2024-10-11 arduino vel from motor_velocities
2024-10-11 rotated laser back to 0
    [dabomb.xacro]
2024-10-11 rotated 180
    [dabomb.xacro]
2024-10-11 rotated laser to 0 degrees
    [dabomb.xacro]
2024-10-11 rotatino again
    [dabomb.xacro]
2024-10-12 Added serial_comm pkg and changed to sub to /motor_vel
2024-10-12 Created a node that directly passes /motor_vel to /arduino_vel
2024-10-12 Created URDF and Robot joint state
    [LIDAR_1.stl, Wheel1_1.stl, Wheel2_1.stl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]
2024-10-12 Add launch for joint state to robot_state_launch
2024-10-13 Moved robot and joint state launch to computer bringup, and fixed the yaml
2024-10-14 Corrected odom and kin lx ly to 0.15
    [mapper_params_online_async.yaml, master.yaml]
2024-10-14 Changed URDF laser from 3.14 to pi
    [dabomb.xacro]
2024-10-14 lidar launch from integration
2024-10-15 rplidar from lidar_test branch
2024-10-18 fix error in debug output
    [config.h, main.cpp]
2024-10-18 last push from the pi
    [LIDAR_1.stl, Wheel1_1.stl, Wheel2_1.stl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]
2024-10-18 arduino readme
2024-10-18 added serial info to arduino readme
2024-10-18 arduino install guide
